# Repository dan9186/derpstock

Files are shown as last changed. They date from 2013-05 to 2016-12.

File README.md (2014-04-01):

Derpstock
=========

A 3D printing deltabot heavily influenced by a Kossel with modifications from Rostock Max, Deltamaker, and others.

All details necessary for building one of your own are included.

Features
========
* V Slot horizontal beams and V Groove Wheels for linear motion
* 300mm capable build area to fit a SeeMeCNC Onyx heated bed
* Capable of over 450mm height build area (a little excessive)
* Easy detached effector and effector arms
* Minimal parts
* Approximately a $600 build

Generating Models
=================
 ## TODO

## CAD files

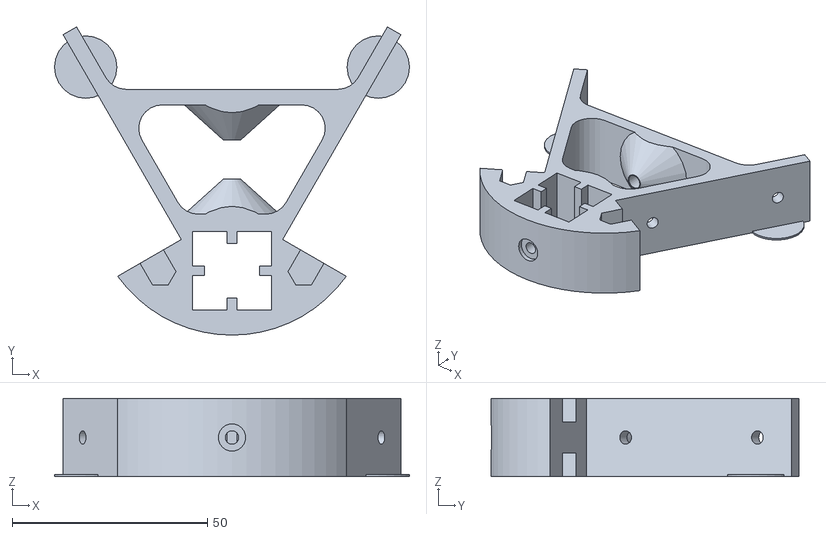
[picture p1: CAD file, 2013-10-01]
frame_vertex.stl
91.0 x 79.0 x 20.0

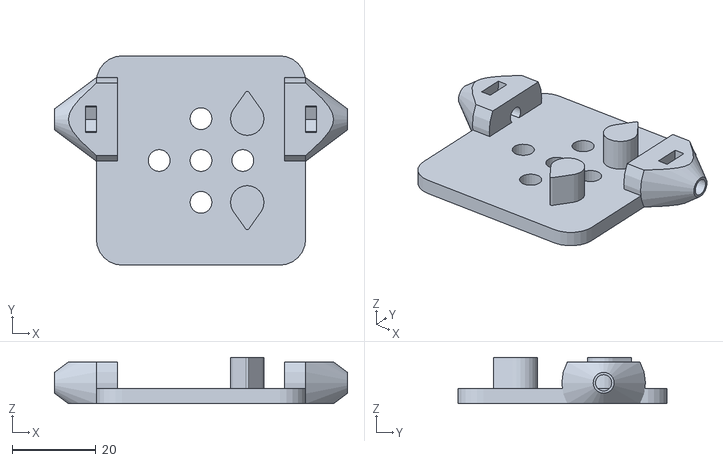
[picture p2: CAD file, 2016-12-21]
output/vslot_carraige.stl
70.0 x 50.0 x 11.1

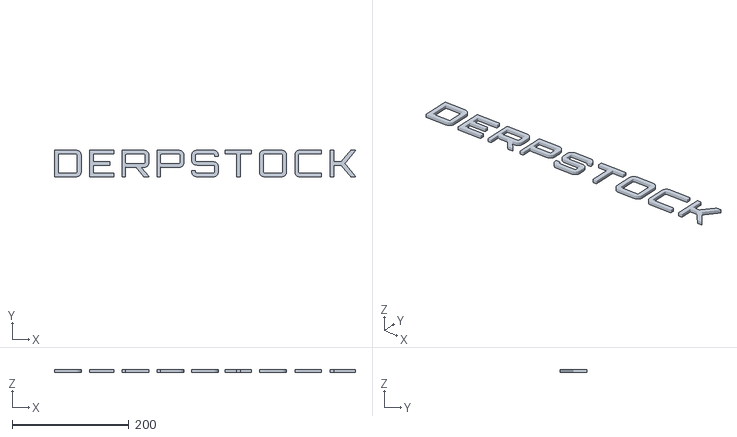
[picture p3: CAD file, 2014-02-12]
src/includes/Derpstock.stl
516.0 x 46.0 x 5.00

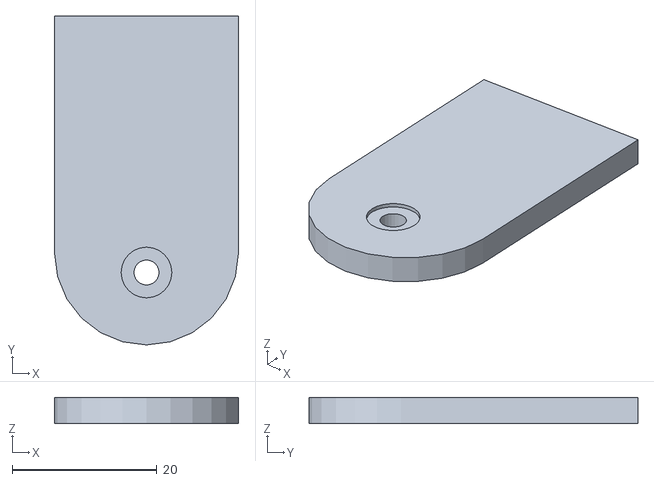
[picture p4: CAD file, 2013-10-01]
glass_tab.stl
25.4 x 45.4 x 3.60

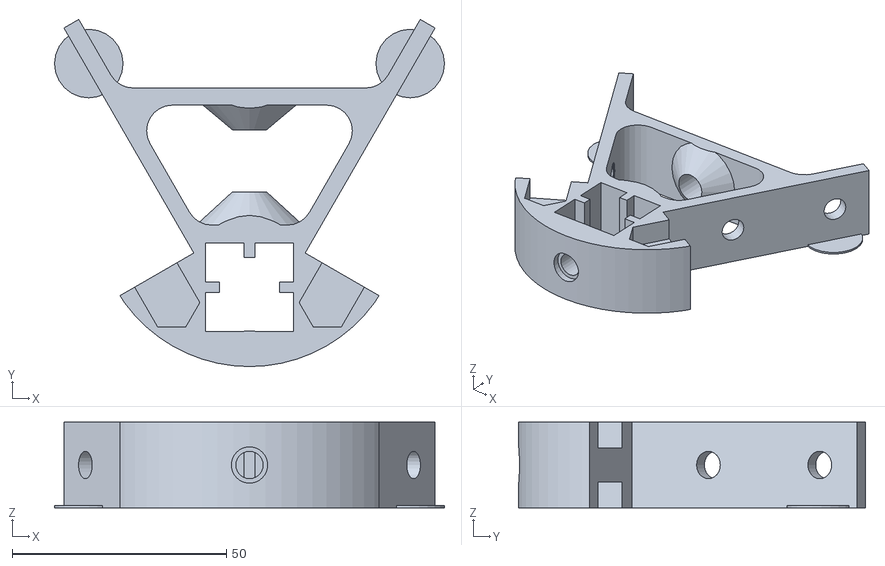
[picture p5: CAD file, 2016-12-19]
output/frame_vertex.stl
91.0 x 81.0 x 20.0

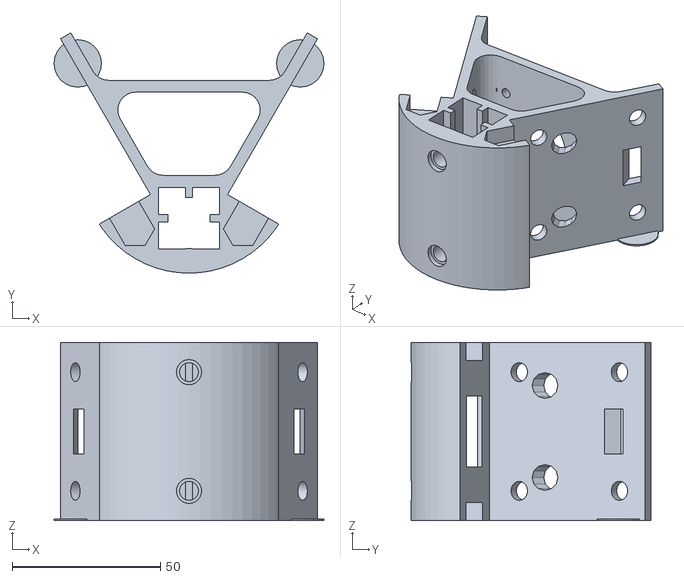
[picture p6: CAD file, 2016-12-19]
output/frame_motor.stl
91.0 x 81.0 x 60.0

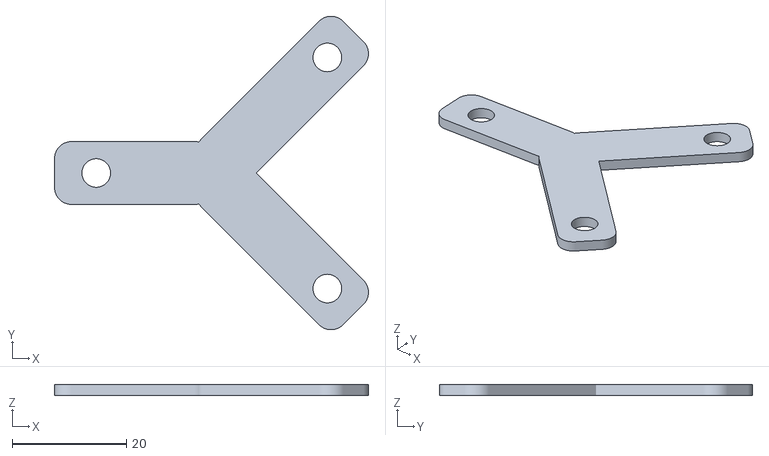
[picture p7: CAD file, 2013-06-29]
vslot_carraige.stl
54.9 x 54.8 x 2.00

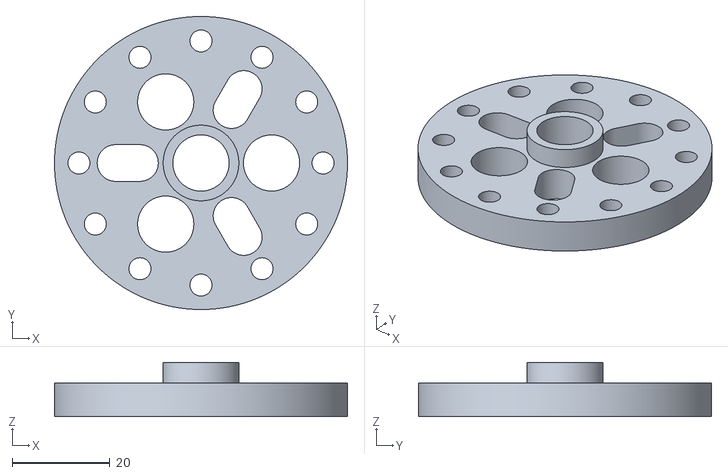
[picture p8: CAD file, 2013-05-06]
hotend_adapter.stl
60.0 x 60.0 x 11.1

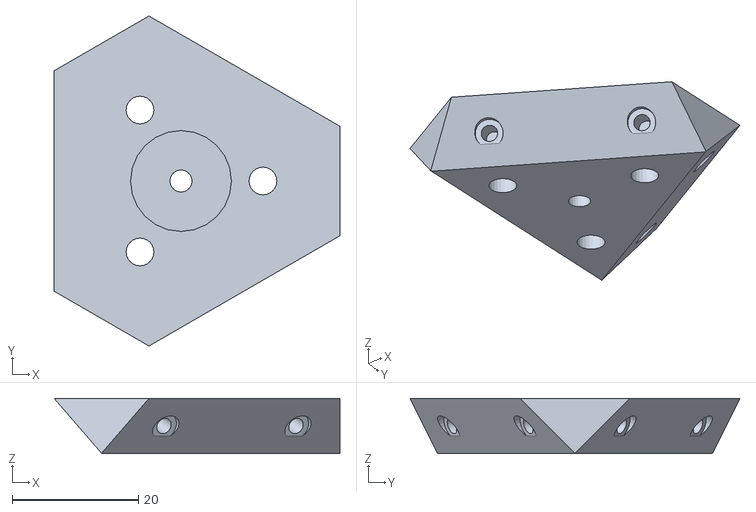
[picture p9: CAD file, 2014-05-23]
output/effector_magnetic.stl
45.3 x 52.3 x 8.75

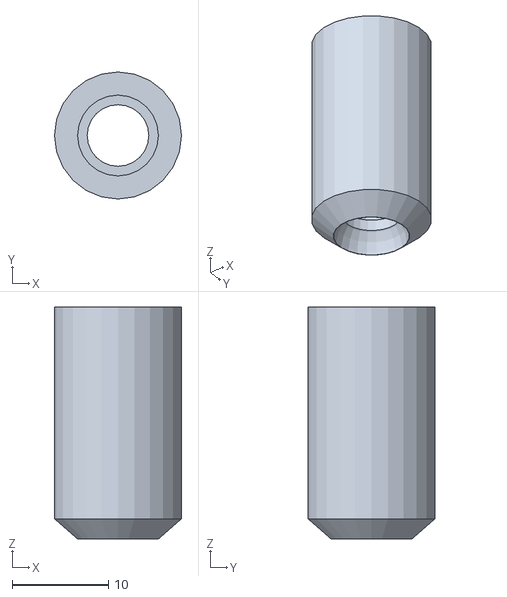
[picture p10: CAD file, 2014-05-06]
output/arm_magnetic_cap.stl
13.2 x 13.2 x 24.1

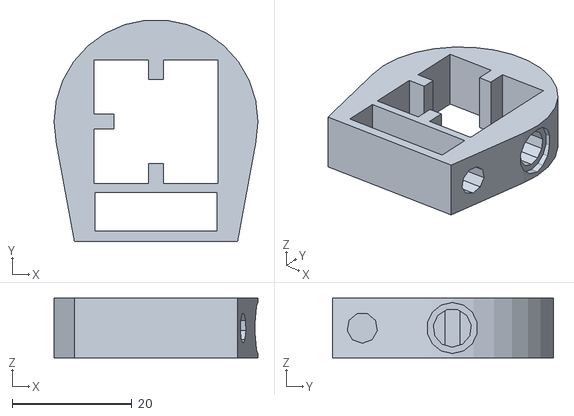
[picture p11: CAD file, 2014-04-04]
output/frame_endstop.stl
34.0 x 36.9 x 10.0

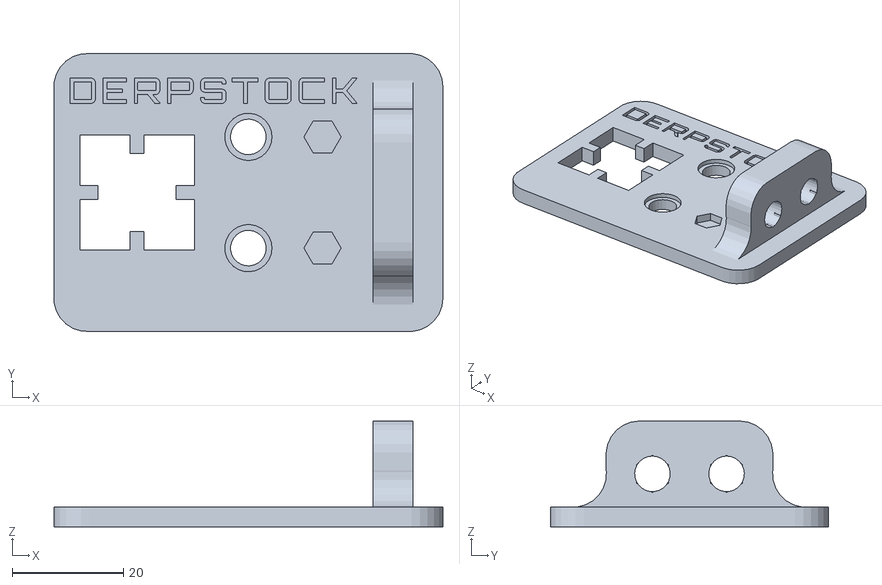
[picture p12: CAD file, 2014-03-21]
output/extrusion_fit_test.stl
70.0 x 50.0 x 19.1

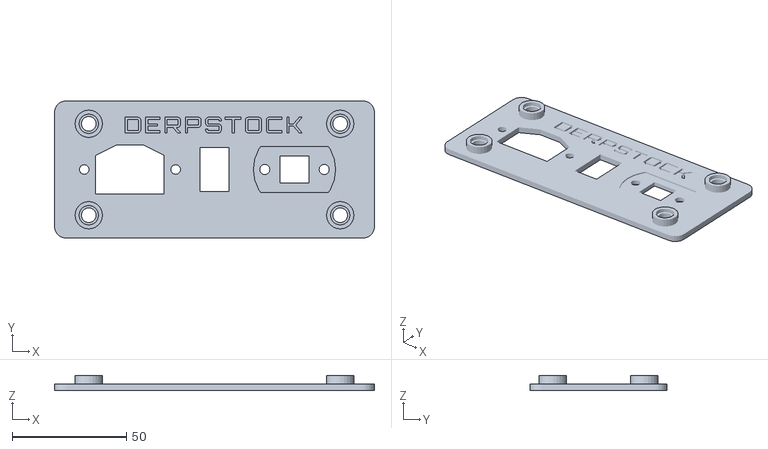
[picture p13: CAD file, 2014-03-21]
output/frame_connector_panel.stl
140.0 x 60.0 x 6.50

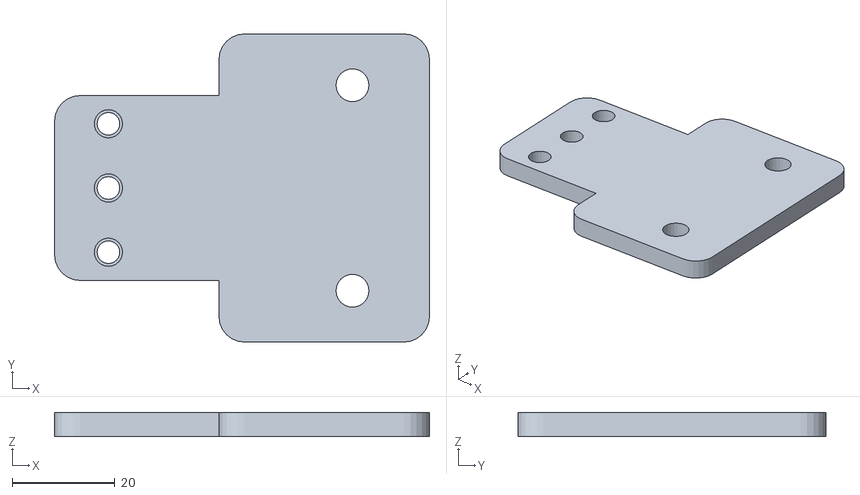
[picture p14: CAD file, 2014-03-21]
output/frame_powersupply_bracket.stl
73.0 x 60.0 x 4.75

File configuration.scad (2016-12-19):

/*
	Authors: Daniel Hess (dan9186)
			 Claudio (orias)
	Git Hub:  https://github.com/dan9186/derpstock
	Original Base: Kossel https://github.com/jcrocholl/kossel
*/

//******* Includes *******//
// More Fontz! by polymaker http://www.thingiverse.com/thing:13677
include <src/includes/Orbitron_Medium.scad>;


//******* Varaibles to Adjust *******//

// Increase to add extra space to holes.
extra_radius = 0.1;
extra_space = 0.1;
extra_extrusion_space = 6*extra_space;

// The diameter and length of the screws needed for the tnuts
tnut_screw_diameter = 5;
tnut_screw_length = 12;

// The width and length of the tnut
tnut_width = 10;
tnut_length = 15;

// Arm parameters
arm_screw_diameter = 4;

// Powersupply Settings
power_supply_width = 122;
power_supply_height = 56;
power_supply_length = 221;
power_supply_screw_diameter = 3;
power_supply_screw_separation = 25;
power_supply_mount_hole_inset = 33;

// NEMA17 stepper motors.
motor_shaft_diameter = 5;
motor_shaft_radius = motor_shaft_diameter/2 + extra_radius;
motor_screw_diameter = 3;

// Placement for the NEMA17 stepper motors.
motor_offset = 44;
motor_length = 47;

// OD = outside diameter, corner to corner.
m3_nut_od = 6.1;
m3_nut_radius = m3_nut_od/2 + 0.2 + extra_radius;
m3_washer_radius = 3.5 + extra_radius;
m3_nut_thickness = 2.4 + 2*extra_space;

// Major diameter of M3 screws for motor
m3_major = 2.85;
m3_radius = m3_major/2 + extra_radius;
m3_wide_radius = m3_major/2 + extra_radius + 0.2;
m3_length = 13;
m3_socket_radius = 3.5;
m3_socket_height = 5;


// Generalized thickness of any walls or tabs
thickness = 3.6;

// OpenBeam or Misumi use 15, for Vslot 20
extrusion = 20;

// Sticky tab to hold glass in place on glass tabs
sticky_width = 25.4;
sticky_length = 25.4;

// Wheel variables for carriage
wheel_separation = 2*(21.39-1.5-0.5);
wheel_diameter=24.39;
wheel_thickness=10.23;

// Gantry variables for carriage
gantry_corner_radius=6.17;
gantry_thickness=6.35;
gantry_height=50;
gantry_width=gantry_height;

gantry_axel_inset_depth=2;
gantry_sm_axel_radius=5/2;
gantry_sm_axel_inset_radius=10.10/2;
gantry_md_axel_radius=7.14/2;
gantry_md_axel_inset_radius=12/2;

gantry_mount_radius=5.02/2;

// Belt variables
belt_width = 5;

// Magnet
magnet_diameter = 8;
magnet_radius = magnet_diameter/2 + 2*extra_radius;

//******* Universal Objects *******//

// Basic 608ZZ bearing
module 608ZZ(){
	difference(){
		cylinder( r=22.1/2, h=7.05 );
		translate( [0,0,-0.25] ) cylinder( r=8/2, h=7.5 );
		translate([0,0,6.05])
		difference(){
			cylinder( r=8/2+5.5, h=1.5 );
			translate( [0,0,-.25] ) cylinder( r=4+1.6, h=2 );
		}
		translate([0,0,-.5])
		difference(){
			cylinder( r=8/2+5.5, h=1.5 );
			translate( [0,0,-.25] ) cylinder( r=4+1.6, h=2 );
		}
	}
}

// Flanged 608ZZ bearing
module F608ZZ(){
	difference(){
		union(){
		cylinder( r=22.1/2, h=7.05 );
		cylinder( r=(22.1+3)/2, h=1-0.1 );
		}
		translate( [0,0,-0.25] ) cylinder( r=8/2, h=7.5 );
		translate([0,0,6.05])
		difference(){
			cylinder( r=8/2+5.5, h=1.5 );
			translate( [0,0,-.25] ) cylinder( r=4+1.6, h=2 );
		}
		translate([0,0,-.5])
		difference(){
			cylinder( r=8/2+5.5, h=1.5 );
			translate( [0,0,-.25] ) cylinder( r=4+1.6, h=2 );
		}
	}
}

// Basic microswitch
module microswitch() {
	difference() {
		union() {
			translate([0, 0, 5])
			cube([19.8+2*extra_space, 6+2*extra_space, 10], center=true);
			translate([2.5, 0.5, 8.5])
			cube([2, 3.5, 5], center=true);
			for (x = [-8, -1, 8]) {
				translate([x, 0, 2.5])
				cube([0.6, 3.2, 13], center=true);
			}
		}
		for (x = [-9.5/2, 9.5/2]) {
			translate([x, 0, 2.5]) rotate([90, 0, 0])
			cylinder(r=2.5/2, h=20, center=true, $fn=12);
		}
	}
}

// NEMA 17 stepper motor.
module nema17() {
	difference(){
		union() {
			translate([0, 0, -motor_length/2]) intersection() {
				cube([42.2, 42.2, motor_length], center=true);
				cylinder(r=25.1, h=motor_length+1, center=true, $fn=60);
			}
			cylinder(r=11, h=4, center=true, $fn=32);
			cylinder(r=2.5, h=48, center=true, $fn=24);
		}
		for (a = [0:90:359]) {
			rotate([0, 0, a]) translate([15.5, 15.5, 0])
			cylinder(r=motor_screw_diameter/2 + extra_radius, h=20, center=true, $fn=12);
		}
	}
}

module nema17_mounts(){
	cylinder(r=11+10*extra_radius, h=20, center=true, $fn=60);
	for (a = [0:90:359]) {
		rotate([0, 0, a]) translate([15.5, 15.5, 0])
		cylinder(r=motor_screw_diameter/2 + extra_radius * 4, h=20, center=true, $fn=12);
	}
}

module screw_socket(screw_diameter, screw_length) {
	// Metric socket cap dimension are
	// socket diameter = 1.5D
	// socket height = 1.25D
	// diameter = D
	// length = L
	union(){
		// Socket cap
		cylinder(r=1.5*screw_diameter/2+5*extra_radius, h=1.25*screw_diameter);
		// Screw shaft
		translate([0,0,-(screw_length+extra_space)])
		cylinder(r=screw_diameter/2+7*extra_radius, h=screw_length+extra_space+1);
	}
}

module extrusion_cutout(h, extra) {
	difference() {
		cube([extrusion+extra, extrusion+extra, h], center=true);
		for (a = [0:90:359]) rotate([0, 0, a]) {
			translate([extrusion/2, 0, 0])
			cube([6, 2.5, h+1], center=true);
		}
	}
}

module vertex_outline( height ){
	difference(){
		union(){
			// Builds the rounded front of the vertex
			intersection(){
				translate([0, 34 - extrusion/2 - 6.5, 0])
				cylinder(r=36, h=height, center=true, $fn=60);
				translate([0, -(50-5.5-extrusion/2), 0]) rotate([0, 0, 30])
				cylinder(r=50, h=height+1, center=true, $fn=6);
			}

			// Builds the triangular back piece of the vertex
			translate([0, 40.5, 0])
			intersection() {
				rotate([0, 0, -90])
				cylinder(r=55, h=height, center=true, $fn=3);
				translate([0, 10, 0])
				cube([100, 100, 2 * height], center=true);
				translate([0, -10, 0]) rotate([0, 0, 30])
				cylinder(r=55, h=height+1, center=true, $fn=6);
			}
		}

		// Remove the material for the extrusion
		extrusion_cutout( height + 2, extra_extrusion_space );

		// Add front screw sockets
		// If there is room for two screws then allow it else do one in the center
		if( height >= extrusion+1.5*tnut_screw_diameter+20*extra_space ){
			for( z=[-1,1] ){
				rotate([90,0,0]){
					# translate([0,z*(height/2-extrusion/2),extrusion/2+15*extra_space+tnut_screw_diameter])
					screw_socket(tnut_screw_diameter,tnut_screw_length);
				}
				translate([0,-(extrusion/2-extrusion/6+2.5*extra_space),0])
				cube([extrusion/3,extrusion/3,height+1], center=true);
			}
		}else{
			rotate([90,0,0]){
				// Socket Screw
				# translate([0,0,extrusion/2+15*extra_space+tnut_screw_diameter])
				screw_socket(tnut_screw_diameter,tnut_screw_length);
			}
			translate([0,-(extrusion/2-extrusion/6+2.5*extra_space),0])
			cube([extrusion/3,extrusion/3,height+1], center=true);
		}
	}
}

module vwheel(){
	rotate([180,0,0])
	translate([0,0,wheel_thickness/2])
	screw_socket(5,25);
	cylinder(r=wheel_diameter/2, h=wheel_thickness, center=true);
}

module mini_gantry(){
    $fn=60;

    difference(){
        hull(){
            for(tb=[-1,1]){
                for(lr=[-1,1]){
                    translate([lr*(gantry_width/2-gantry_corner_radius),tb*(gantry_height/2-gantry_corner_radius),0])
                    cylinder(r=gantry_corner_radius, h=gantry_thickness);
                }
            }
        }

        // mounting holes
        translate([0,0,-0.5]){
            cylinder(r=gantry_mount_radius, h=gantry_thickness+1);
            for(lr=[-1,1]){
                translate([lr*10,0,0])
                cylinder(r=gantry_mount_radius, h=gantry_thickness+1);
                translate([0,lr*10,0])
                cylinder(r=gantry_mount_radius, h=gantry_thickness+1);
            }
        }

        // wheel mounts
        for(lr=[-1,1]){
            translate([0,0,-0.5]){
                translate([lr*(-gantry_width/2+9.05),-gantry_height/2+9.05,0]){
                    cylinder(r=gantry_sm_axel_radius, h=gantry_thickness+1);
                    translate([0,0,gantry_thickness-gantry_axel_inset_depth+0.5])
                    cylinder(r=gantry_sm_axel_inset_radius, h=gantry_axel_inset_depth+1);
                }
                translate([lr*(-gantry_width/2+9.05),gantry_height/2-10,0]){
                    cylinder(r=gantry_md_axel_radius, h=gantry_thickness+1);
                    translate([0,0,gantry_thickness-gantry_axel_inset_depth+0.5])
                    cylinder(r=gantry_md_axel_inset_radius, h=gantry_axel_inset_depth+1);
                }
            }
        }
    }
}

module derpstock_logo(){
	// steps - the amount of detail, the higher the more detailed.
	// center - whether the output is centered or not
	// extra - extra distance between characters
	// height - height of extrusion, 0 for 2d
	import("./includes/Derpstock.stl");
}

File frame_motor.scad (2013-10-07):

include <configuration.scad>;

$fn = 24;

module frame_motor() {
	motor_mount_height = 3*extrusion;
	translate([0,0,motor_mount_height/2])
	union(){
		// Pad to improve print bed adhesion for slim ends
		translate( [-37.5, 52.2, -motor_mount_height/2] ) cylinder(r=8, h=0.5);
		translate( [37.5, 52.2, -motor_mount_height/2] ) cylinder(r=8, h=0.5);
	
		difference(){
			// Base vertex shape
			vertex_outline( 3*extrusion );
	
			// Pully cutout
			difference() {
				translate([0, 60.5, 0])
				minkowski() {
					intersection() {
						rotate([0, 0, -90])
						cylinder(r=55, h=3*motor_mount_height+1, center=true, $fn=3);
						translate([0, -32, 0])
						cube([100, 16, 3*motor_mount_height+1], center=true);
					}
					cylinder(r=6, h=1, center=true);
				}
			}
	
			// Motor mounting space cutout
			translate([0, 60.5, 0]) minkowski() {
					intersection() {
					rotate([0, 0, -90])
					cylinder(r=55, h=3*motor_mount_height+1, center=true, $fn=3);
					translate([0, 7, 0])
					cube([100, 30, 3*motor_mount_height+1], center=true);
				}
				cylinder(r=6, h=1, center=true);
			}
	
			// Motor mount cutouts
			translate([0,46.5,0]) rotate([90,0,0]) nema17();
	
			for(lr=[-1, 1]) {
				// Side screw cutouts
				for(z=[-1,1]){
					translate( [0,-30,z*(motor_mount_height/2-extrusion/2)] )
					rotate([0, 0, 30*lr]) {
						for(y=[51, 90]) {
							# translate([lr*11.4, y, 0]) rotate([0, lr*90, 0])
							screw_socket(tnut_screw_diameter, tnut_screw_length);
						}
					}
				}
	
				// Nut tunnels
				rotate([0, 0, 30*lr]) 
				translate([-16*lr, 111, 0]) {
					translate([0, -99.5,0]){
					// Repeat the same thing for top and bottom
						for (z = [-1, 1]){
							hull(){
								translate([0,2.5,z*(motor_mount_height/2-0.5)])
								rotate([0, 0, -lr*30])
								cylinder(r=4, h=extrusion/2+1, center=true, $fn=6);
								translate([0,-2.5,z*(motor_mount_height/2-0.5)])
								rotate([0, 0, -lr*30])
								cylinder(r=4, h=extrusion/2+1, center=true, $fn=6);
							}
						}
	
						hull(){
							translate([0,2.5,0])
							rotate([0, 0, -lr*30])
							cylinder(r=4, h=2*motor_mount_height/3, center=true, $fn=6);
							translate([0,-2.5,0])
							rotate([0, 0, -lr*30])
							cylinder(r=4, h=2*motor_mount_height/3, center=true, $fn=6);
						}
					}
				}
			}
	
			// Logo for the front side of the object
			*translate([20,-extrusion/2,0]) rotate([90,-90,30])
			scale([0.1,0.1,1]) derpstock_logo();
	
			% extrusion_cutout( motor_mount_height+20, extra_extrusion_space );
		}
	}
}

frame_motor();

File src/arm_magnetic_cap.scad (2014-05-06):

include <../configuration.scad>;

$fn = 24;

module magnetic_cap(){
	translate([0,0,22+magnet_diameter/4])
	rotate([180,0,0])
	difference(){
		union(){
			cylinder(r=magnet_radius+thickness*2/3, h=22);

			translate([0,0,22])
			cylinder(r1=magnet_radius+thickness*2/3, r2=magnet_radius, h=magnet_radius/2);
		}
		translate([0,0,22+magnet_diameter/2-1.75])
		sphere(r=magnet_radius);

		cylinder(r=magnet_radius-1, h=22+1);

		translate([0,0,-1.75])
		cylinder(r=magnet_radius, h=22);
	}
}

magnetic_cap();

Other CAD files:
output/hotend_adapter.stl
output/frame_support.stl
output/frame_ramps.stl
output/frame_glass_tab.stl
src/frame_motor.scad
extrusion_fit_test.scad
frame_endstop.scad
frame_vertex.scad
glass_tab.scad
src/effector_magnetic.scad
src/extrusion_fit_test.scad
src/frame_connector_panel.scad
src/frame_endstop.scad
src/frame_glass_tab.scad
src/frame_powersupply_bracket.scad
src/frame_ramps.scad
src/frame_support.scad
src/frame_vertex.scad
src/hotend_adapter.scad
src/includes/Orbitron_Medium.scad
src/vslot_carraige.scad

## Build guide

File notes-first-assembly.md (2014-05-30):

#Notes- First Assembly#

##Tools
* Ball-end Metric Hex key set
* Rubber mallet (optional)
* M5 drill bit (optional)
* ~1/2" binder clips (3 or 6) to mount bed.

##Part Notes

###Frame Motor
* M3 8mm are perfect (steppers)
* M3 screw holes need to have enough clearance to drop through
* M5 14mm work for the vertical vslot anchors
* M5 10mm crossbeam vslot NO WASHERS
* M5 12mm crossbeam vslot WITH WASHERS
* Vslot cutouts almost perfect, self cleaning
* Use the M4(3mm) driver to space the pulley away from the vertex to align the belt path 

###frame_vertex
* M8 screw cuts threads well for the first portion, and well enough for the second. 
* M5 14mm work for the vertical vslot anchors
* Vslot cutouts almost perfect, self cleaning
* Order of operations: Crossbeam tslot installation before M8 idler pulley installation.

## Crossbeam lengths

### Mounting Plate 3 Points of Contact

* Crossbeam lengths (214mm*2)=428mm crossbeams (212-213mm)
* :. Vertical beam = 644mm (~425-500mm Z height)
* One 1500mm Vslot length will yield ((2*428mm)+644mm)

## Assembly

* Cut slowly, less cleanup
* When assembling vertices, assemble snug, loosen afterthings are together, square up then tighten.
* 

## Working cuts

* Misuimi 428mm (9 cross bars)
* Vslot 1M (3 vertical bars)
* Effector Arms
    * Roughly 75% of 8mm 50mm carbon rod (318mm + 2x(endcaps + screw balls (dan estimate 42mm added) (cd estimate 56mm added))) 
## Bed mounting 

* M5 12mm (currently unless we countersink) low profile (openbuilds)

## Assembling Triangles

* 2 assemblies (bar, vertex, bar) & (vertex, bar, vertex)
* Double flanged bearings (2xF608ZZ)
* The double flanged bearings are to be installed last.

## Assembling uprights

* All vertical bars need to be flush with the bottom surface
* 

## Vertical bar considerations

* 750mm seems to be the sweet spot
* 1m has wobble
* 

# Mechanical notes

## Assembling Arm

* 

## Motors

* Derpstock nameplate is front and center
* X motor Front right
* Y motor Front Left
* Z motor Rear Center
* Movement of effector plate follows traditional XY movement
* 

# Wiring

## Effector
* 10 pin connector at the base for effector wiring or:
* 6 Pin connector at the base for effector wiring (bed leveling)
    * 2 pins for microswitch
    * 3 pins for Servo
        * Servo and cooling fan share ground
    * 2 pins for fan
* 4 pin connector for hot end
    * 2 pins for hot end
    * 2 pins for thermistor

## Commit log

2013-05-06 hotend adapter from SeeMeCNC modified to include spacer
    [hotend_adapter.scad]
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2013-05-06 fixed stl file
    [hotend_adapter.stl]
2013-05-13 adding configuration file to house constants and base functions
    [configuration.scad]
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2013-09-27 designated sections to the configuration file, ensured all the latest items from kossel's configuration
    [configuration.scad]
2013-09-27 added orbitron medium font scad file and created logo function
    [Orbitron_Medium.scad, configuration.scad]
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2013-09-27 added more generic shapes for sets of parts
    [configuration.scad]
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2013-09-28 corrected vertex_outline issue with extrusion width
    [configuration.scad]
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2013-09-30 created a small piece to print for testing the fit with different size extrusions and determining the extra space needed
    [extrusion_fit_test.scad, extrusion_fit_test.stl]
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2013-09-30 removed unnecessary lines by changing background to debug for showing model and still removing material
    [frame_vertex.scad]
2013-09-30 found extra line that was commented out and not needed
    [frame_vertex.scad]
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2013-09-30 resolved Issue #1 by adjusting the translation to the cone to include the extra_radius width added to the extrusion cutout
    [frame_vertex.scad]
2013-09-30 corrected rendering issues with the nut tunnels by removing irrelevant objects and set model to start flat on the plane not centered
    [frame_vertex.scad]
2013-10-01 differentiated extra_radius and extra_space for use with radial vs linear object measurements
    [configuration.scad]
2013-10-01 updated screw cutout origin to be at the base of the screw socket bottom and updated frame_vertex to use the changes
    [configuration.scad, frame_vertex.scad]
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2013-10-01 updated stls to match changes to scad models
    [frame_vertex.stl, glass_tab.stl]
2013-10-01 removed front screw holes from frame_vertex and added to vertex_cutout module in configuration
    [configuration.scad, frame_vertex.scad]
2013-10-01 modified nema module to automatically provide its own cutouts and completed frame_motor
    [configuration.scad, frame_motor.scad]
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2013-10-01 slight modifications in prep for future changes to screw sizes
    [configuration.scad]
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2013-10-02 adjusted extra spacing for smooth insertion, (4.5x extra_radius)
    [extrusion_fit_test-4-5xER.stl, extrusion_fit_test.scad]
2013-10-03 Added extrusion fitting variable to extrusion_fit and configuration.scad
    [configuration.scad, extrusion_fit_test.scad]
2013-10-07 removed unnecessary stl, updated fit test to handle other items, exported latest stl
    [extrusion_fit_test-4-5xER.stl, extrusion_fit_test.scad, extrusion_fit_test.stl]
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2013-10-07 Issue #6 was mostly corrected by attrition, also corrected extra_extrusion_space in process
    [frame_motor.scad, frame_vertex.scad]
2013-10-07 Work on Issue #3 to generalize screws
    [configuration.scad, frame_endstop.scad, frame_motor.scad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]
2013-10-08 updated structure to support automated stl generation and generated latest stls
    [Orbitron_Medium.scad, configuration.scad, extrusion_fit_test.scad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]
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2013-10-08 generalized screw sizes in fit test and resolving Issue #3
    [extrusion_fit_test.scad, extrusion_fit_test.stl]
2013-10-08 updated fit test to only use variables from configuration.scad and completing Issue #7
    [configuration.scad, extrusion_fit_test.scad]
2013-10-08 parameterized the nut channels in frame_motor and frame_vertex, updated nut channel to fit vslot tnut
    [configuration.scad, frame_motor.scad, frame_motor.stl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]
2013-10-08 lessed complexity of pully cutout on frame_motor, separated nema17 and nema17 motor mount cutouts, improved overall fast rendering of frame_motor
    [configuration.scad, frame_motor.scad]
2013-10-08 improved rendering of frame_motor and frame_vertex, added wiring access to frame_motor
    [frame_motor.scad, frame_vertex.scad]
2013-10-08 reenabled logo text in the side of the model
    [frame_motor.scad]
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2013-10-22 updated additional radius space for screw socket module
    [configuration.scad]
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2013-10-23 updated stl files to use latest model changes
    [extrusion_fit_test.stl, frame_endstop.stl, frame_motor.stl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]
2013-10-24 added arm mounting points to carriage and rewriting based on parameters from configuration
    [configuration.scad, vslot_carraige.scad]
2013-11-06 updated idler cones to be 1mm longer and adjusted the idler screw hole for a 608zz resolving Issue 18 and Issue 19
    [frame_vertex.scad]
2013-11-12 expanded back side of idler to not needed tapping
    [frame_vertex.scad]
2013-11-12 modified wire access to help with splitting, adjusted spacing on nut tunnels
    [frame_motor.scad]
2013-11-12 removed cut out on extrusion from the front screw side to resolve Issue #17
    [configuration.scad]
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2013-11-12 converted carriage to use extrusion for base size, added belt details to configuraiton
    [configuration.scad, vslot_carraige.scad]
2013-11-15 added M3 screw holes and nut traps to arm mounts on carriage
    [vslot_carraige.scad]
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2013-11-20 partial solution to Issue 16 by widening the arc on the front to make more flush with extrusion
    [configuration.scad]
2013-11-20 Remaining modifications to adjust nut tunnels further out for Issue #16
    [frame_motor.scad, frame_vertex.scad]
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2014-01-21 Added screw/toolpath holes to aid in stepper motor mounting.
    [derpstock_frame_motor-stepper-tool-holes.stl]
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2014-02-02 Update configuration.scad
    Adding extra clearance for M3 stepper mounts
    [configuration.scad]
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2014-02-03 Resizing screw holes for better fit for Issue #31
    Adding +4 extra_radius to screw shaft spacing and +2 extra_radius to screw cap spacing for a better fit. Resolves Issue #31.
    [configuration.scad]
2014-02-03 Adding 0.1 extra to extrusion cutout for Issue #29
    Increasing by +1 extra_space after further test fitting to help with getting the pieces started on the extrusion.
    [configuration.scad]
2014-02-04 elongating nut tunnel for Issue #33
    [frame_motor.scad, frame_vertex.scad]
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2014-02-04 updated idler cone spacing to be a little tighter
    [frame_vertex.scad]
2014-02-04 converted test piece to branch and improve hole rendering
    [derpstock_frame_motor-stepper-tool-holes.stl, frame_motor.scad, frame_motor.stl]
2014-02-04 test piece has been integrated as part of motor_access branch
    [derpstock_frame_motor-stepper-tool-holes.stl]
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2014-02-05 created a base of support beam for issue #38
    [frame_support.scad]
2014-02-05 expanded hole slightly to ensure good clearance
    [frame_motor.scad]
2014-02-05 updated microswitch module to render better, start of remodle of endstop holder
    [configuration.scad, frame_endstop.scad]
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2014-02-11 updating source files and removing an irrelevant one
    [extrusion_fit_test.stl, frame_endstop.stl, frame_motor.stl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]
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2014-02-12 added integrated connector panel mount to resolve issue #43
    [frame_connector_panel.scad]
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2014-02-12 added derpstock logo as static item to resolve issue #12
    [Derpstock.stl, configuration.scad]
2014-02-12 resolved issue #46
    [frame_ramps.scad]
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2014-02-12 more standardization even if it's wrong
    [frame_glass_tab.scad]
2014-02-12 resolving issue #39
    [configuration.scad, frame_powersupply_bracket.scad, frame_powersupply_bracket.stl]
2014-02-12 resolving issue #47
    [frame_connector_panel.scad, frame_connector_panel.stl]
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2014-02-14 began redesign of vslot carriage making it much easier to implement
    [configuration.scad, vslot_carraige.scad]
2014-02-14 added belt clamps and migrated some settings to the config file
    [vslot_carraige.scad]
2014-02-14 Adjusting horizontal screw holes for Issue #52
    [frame_support.scad]
2014-02-14 Shrunk panel by 20mm to assist with peeling issues
    [frame_connector_panel.scad]
2014-02-15 adding current work on a support for ball bearings
    [vslot_carraige.scad]
2014-02-15 merging frame support modifications made in wrong branch
    [frame_support.scad]
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2014-02-26 corrected sizing
    [frame_powersupply_bracket.scad]
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2014-02-26 corrected power supply screw hole size
    [configuration.scad]
2014-02-26 added center mount hole for power supply, single piece works still
    [frame_powersupply_bracket.scad]
2014-03-17 added arm mounts and screw holes for arms
    [vslot_carraige.scad]
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2014-03-19 Adjusting wheel separation
    Adjusting the wheel separation for Issue #55
    [configuration.scad]
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2014-03-21 fixing the wheel separation to use the config variable
    [configuration.scad, vslot_carraige.scad, vslot_carraige.stl]
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2014-03-21 the wheels were just a slight bit too tight
    [configuration.scad, vslot_carraige.stl]
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2014-04-01 updating new endstop mount for issue #56
    [configuration.scad, frame_endstop.scad]
2014-04-01 adding adhesion pads for Issue #53
    [frame_ramps.scad]
2014-04-01 increased belt clamp height for issue #62
    [vslot_carraige.scad]
2014-04-01 rearranged arm mounts for magnets for Issue #64
    [vslot_carraige.scad]
2014-04-04 correcting ball join screw error
    [vslot_carraige.scad]
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2014-05-06 was able to shrink it a bit more
    [effector_magnetic.scad, effector_magnetic.stl]
2014-05-23 formatting fix, and flipped piece
    [effector_magnetic.scad, effector_magnetic.stl]
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2014-05-30 increased insulator diameter to help press fit better
    [effector_magnetic.scad]
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
